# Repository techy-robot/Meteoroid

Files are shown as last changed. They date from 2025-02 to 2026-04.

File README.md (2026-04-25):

# Meteoroid


Production-ready 3d printer based on a Ender 5 frame, with multifunction tool changing, bed changing, and accessories with robots.

Preview Picture
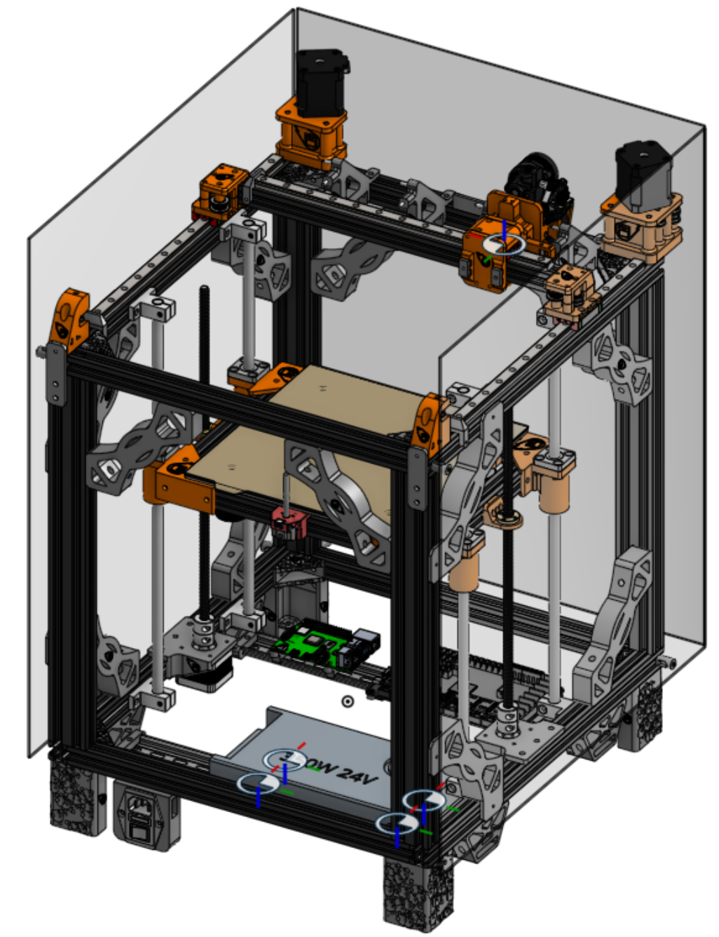
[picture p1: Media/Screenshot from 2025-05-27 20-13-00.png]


Latest V0.7.0 [Onshape Link](https://cad.onshape.com/documents/1de0655c0501c319c0be82e5/v/c2a582b56fbe86c2e3bf18a1/e/f03e8779d1a8cc2741025c01)

It is desktop machine with plug and play heads. Chain these machines together and add robot carriages in between and you got yourself an awesome modular factory that can fit on a bench. The cost of the _entire system_ will likely be several thousand dollars, with the main machine between $300 to $500. I aim to lower the cost of a complete industrial system as much as possible.

The base machine is a CoreXY printer with a 500+mm/s move speed 30k+ accel, and 4 tool changer slots. The printer can be partially enclosed, with openings for robots to quick swap tools and beds and sometimes even sub-tools (Like a PnP head with different nozzle sizes). Software-wise, it will be running Klipper, which can interface with other software like OpenPNP using macros and linux ports.

Features:
- Standard 235mm x 235mm heated bed size with Garolyte bed for easy print release, supported by dual z-axis motors to provide stabilty without the complexity of an automatic leveling trimotor bed.
- Klipper
- Tool changer with 4 slots
- CoreXY
- Medium cost desktop production system
- Completely Open-Source
- 3 Accessory slots for extra toolhead elements like PnP heads or a camera
- Off-the-shelf components that are well known and high-quality, with many parts 3D printed in ASA
- Optional enclosure
- High print speed 500mm/s and 30k accel

I also designed a little adapter board I called Klipper to CACKLE. It basically takes USB-c input and 24v power, and converts this to my [CACKLE](https://github.com/techy-robot/CACKLE) layout spec and RS485 communication protocal. It uses a CH32 chip to process the commands and output equivalent Luos spec datapackets over the bus to my system.
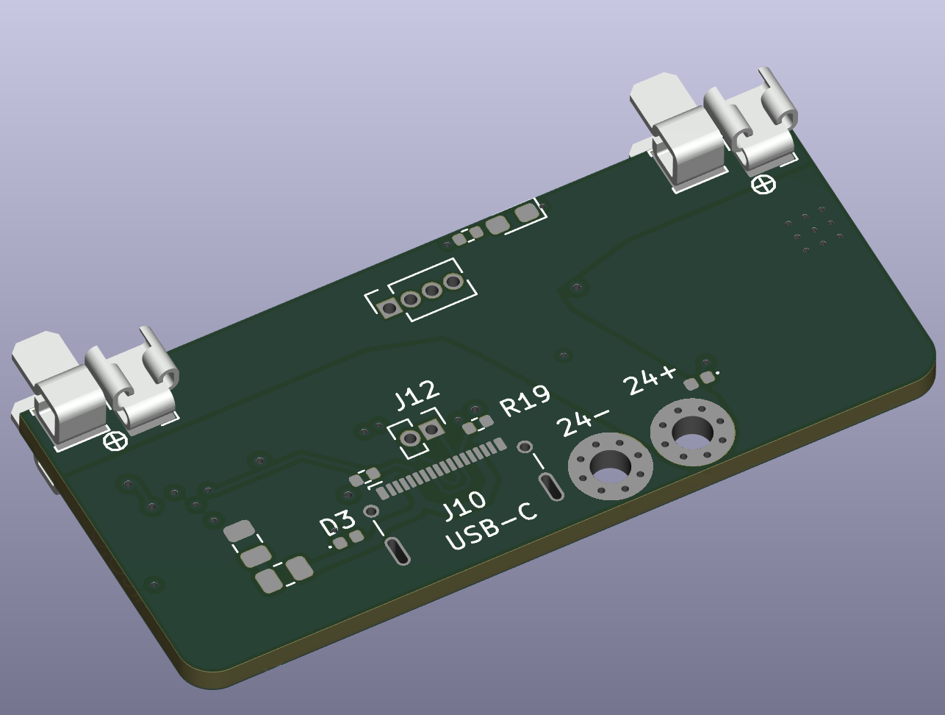
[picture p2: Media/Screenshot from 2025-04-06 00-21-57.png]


# Building
I don't have specific build instructions yet as that takes a lot more development time, but you can reference the [BOM](https://github.com/techy-robot/Meteoroid/blob/main/BOM_Main%20assembly_simplified.csv) and the CAD file/Onshape to get all the parts and build it.

# Development Log
This project was worked on sporadically since Feb 1, 2025

See [Changelog](https://github.com/techy-robot/Meteoroid/blob/main/Changelog.md) for my full development log and the nitty-gritty details

# Credits
The motion system inspiration is from [Zero G Mercury 1.1](https://docs.zerog.one/manual/build/mercury_eva), which is a relatively simple corexy conversion for ender 5-style frames. I have tweaked many of the parts to fix small issues I noticed, revamped the frame with supports, added a toolchanging solution, and a 2 axis bed leveling system instead of the more costly 3-axis Hydra solution. The toolchanger is similar to the [Daksh V2](https://github.com/ankurv2k6/daksh-toolchanger-v2/) solution, except with a simpler single lock system, and concentric kinematic mount points instead of asymetrical contact mounts.

Everything else should be my own design, from the upcoming bed changing solution, upcoming robotic arms, toolheads, and the asteroid texture used on some of the parts.

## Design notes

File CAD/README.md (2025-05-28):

This folder is for CAD documents and step files. Their is no reason to have the individual parts when there is an assembled version available, so I have only included the main assembly as well as specific toolheads. Check out the STLs folder for the individual 3D printed parts.

Also, for the sake of Github some files have been compressed.

To view the entire CAD design, checkout the latest [Onshape document](https://cad.onshape.com/documents/1de0655c0501c319c0be82e5/w/00a76129439a8316e13df1dd/e/f03e8779d1a8cc2741025c01).

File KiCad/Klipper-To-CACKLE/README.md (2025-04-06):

---
modified: 2025-04-05T19:11:32-07:00
---

# Klipper to Cackle

This is a simple adapter board PSU that takes 24v in and usb, and outputs a CACKLE compatible form factor and RS485 Luos commands.

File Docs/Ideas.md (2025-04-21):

- Add a vslot extrusion and wheels for switching off beds. Line up the rails and roll a new bed on
- Hotswap toolheads aren't supported in klipper, so either add this feature or create a macro that modifies the config and reboots klipper each toolrow swap.
- Pogo pins for USB and CAN bus between toolhead an motion carrage
- Use only USB 2.0 to communicate between MCUs because its faster than CAN bus and can support more than klipper data (like hubs and cameras). It also is easier to connect and hotswap, there aren't any resistor configuration requirements. I can use USB 3.0 for static hubs that don't change
- Design a simple converter PCB from XT60 connector and USB C, to the molex special connector
- Design hotswap pcb connectors
- Use JLCMC for all my fasteners, and mcmaster carr for other things
- Don't use Obico for failure detection, I need something on the pi like [Forgetti](https://github.com/willuhmjs/forgetti), [3d Print Sentinel](https://github.com/oliverbravery/3D-Print-Sentinel), Scythe-Spaghetti-detection or [PiNozCam](https://github.com/DrAlexLiu/OctoPrint-PiNozCam)

# Tools
dremel
spindle + drill
spindle + milling flute/ball nose mill
router bit
mini sawblade
spindle with grinding wheel / cup
tapmatic-style tap holder
shaper cutter
microscope camera
inkjet cartridge
waterjet cutter
plasma cutter
pencil
exacto holder
glass cutter
sharpie
vibropeen
lasercutter
syringe dispenser
brush + paint pots
hand file
fiber laser holder
mirror X/Y stage
plate-in-place electrode
CMM stylus probe holder
hotwire foam cutter holder
pick-and-place suction tool
soldering iron (w\ solder dispenser ?)
EDM electrode holder

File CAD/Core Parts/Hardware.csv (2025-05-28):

Name | Variable type | Value | Description
M3_screw_hole | Length | 3.15
M3_tight_screw_hole | Length | 3
M3_screwhead_hole | Length | 6
M3_heatset_hole | Length | 4.7
M3_heatset_depth | Length | 5
M5_screw_hole | Length | 5.2
M5_tight_screw_hole | Length | 4.9
M5_screw_head_hole | Length | 9
M4_screwhole | Length | 4.2
M4_screw_head_hole | Length | 8
M4_tight_screw_hole | Length | 4
M4_heatset_hole | Length | 5.7
Dowel_pin_dia | Length | 5.2
belt_width | Length | 6
belt_thickness | Length | 1.38
belt_tooth_thickness | Length | 0.75
belt_other_thickness | Length | 0.63 | the non-tooth thickness of belt
ABS_tolerance | Length | 0.2
smooth_idler_dia | Length | 13
toothed_idler_dia | Length | 12.22
belt_gap | Length | 1.5 | gap btw belt and plastic parts
smoothed_idler_9mm_flange_stack | Length | 11.2
toothed_idler_9mm_stack | Length | 9.5
motion_gap | Length | 1.5
magnet_diameter | Length | 6.35
magnet_depth | Length | 3.175
guide_with_screw_depth | Length | 1.4 | Guides are what keeps a part in alignment in an X extrusion. with nut is the depth with a screw going through it
guide_depth | Length | 4
guide_width | Length | 5.8 | width of beam, some tolerance

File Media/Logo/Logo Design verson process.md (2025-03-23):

# Inkscape Notes
- You can convert paths to filled objects using union and strokes or objects to paths and all sorts of fun combos
- If you go into object properties you can custom name SVG items!
- Use Path Combine or Break Apart tools to give paths a common stroke and color, even if they aren't connected. Boolean ops are for connections

# Process for creating Logo types
1. Create the base color logo. Use offset live path effect with rounded corners and then flatten it to a normal object for the internal light colors. More control than the Path Outset tool. Break it apart and delete the weird extra small shapes. Make sure to name all objects, and have a layer for the printer and layer for the burn
2. Copy and start on two-tone version. Delete the 3rd inset color. Make sure the color pallet only has Primary and Background colors. Change all lines to Primary color, and make sure everything else is a fill color. Re-create the burn internal offset except without internal edges. The burn has to go behind the printer now.
3. Copy and start on black and white version. Only change necessary, which should just be the colors
4. For Mono, take the path difference of the trail and the background so that you have no background fill object. Delete the fill object for the printer. Now it should be transparent and have only one color
5. Finally, to get a logo that can be extruded in 3D, convert all strokes to paths, boolean union on all paths, Get ride of all groups and layers, and save as a DXF R14 file without changing any of the defaults.

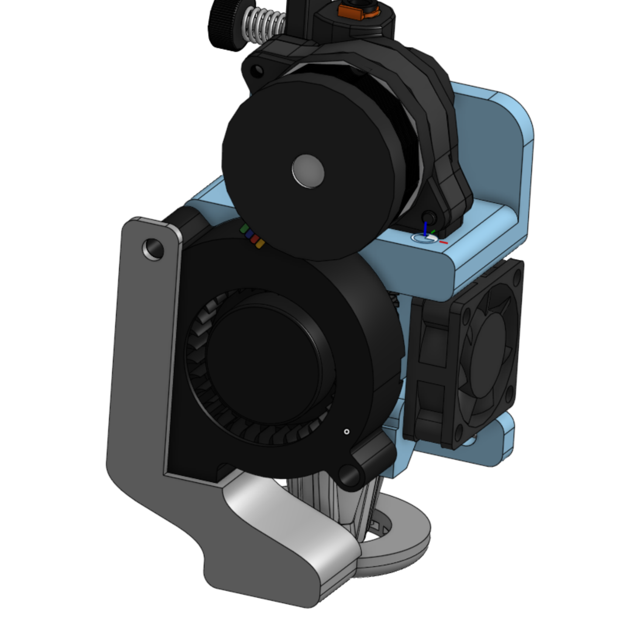
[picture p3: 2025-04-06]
Media/Screenshot from 2025-04-04 20-28-48.png

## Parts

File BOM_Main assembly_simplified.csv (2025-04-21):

ID | Quantity | Description | Name | Already have? | 3D printed | Price | Purchase Link
 | 1 |  | Left X joint bottom |  | t
 | 1 |  | Left X joint top |  | t
 | 1 |  | Right X joint bottom |  | t
 | 1 |  | Right X joint top |  | t
 | 2 |  | Z+AC0-Axis Motor Inside Bracket |  | t
 | 2 |  | bed +AC0- linear bearing mount corner |  | t
 | 2 |  | bed +AC0- linear bearing mount corner mirror |  | t
 | 4 |  | bed +AC0- frame mount |  | t
 | 2 |  | bed +AC0- lead screw nut mount |  | t
 | 4 |  | bed +AC0- thumb screw |  | t
 | 1 |  | Z endstop mount |  | t
 | 4 |  | base standoff |  | t
 | 4 |  | DIN rail drop |  | t
 | 2 |  | DIN rail clip +AC0- LRS200 LRS350 |  | t
 | 2 |  | DIN rail clip +AC0- Octopus pro |  | t
 | 4 |  | frame stiffener side mount |  | t
 | 8 |  | frame stiffener |  | t
 | 1 |  | Left Motor Mount |  | t
 | 1 |  | Left Motor Mount Top |  | t
 | 1 |  | Left Tensioner |  | t
 | 1 |  | Right Motor Mount |  | t
 | 1 |  | Right Motor Mount Top |  | t
 | 1 |  | Right Tensioner |  | t
 | 2 |  | Tensioner Plate |  | t
 | 2 |  | DIN rail clip +AC0- RPI4 |  | t
 | 1 |  | PSU switch mount |  | t
 | 1 |  | Carraige +AC0- back plate |  | t
 | 2 |  | Carraige +AC0- Belt clampx2 |  | t
 | 1 |  | Carraige +AC0- bottom |  | t
 | 1 |  | Carraige +AC0- front belt plate |  | t
 | 1 |  | Carraige +AC0- lock clamp |  | t
 | 1 |  | Carraige +AC0- lock slider |  | t
 | 1 |  | Carraige +AC0- Rail mount |  | t
 | 1 |  | Carraige +AC0- spring plate |  | t
 | 1 |  | Rapido Orbiter Toolhead +AC0- mount |  | t
 | 1 |  | Rapido Orbitor Toolhead +AC0- Duct |  | t
 | 4 |  | Tool Bay +AC0- Basic |  | t
 | 3 |  | Rail End Stop |  | t
1 | 4 | 370mm beam | 2020 extrusion 370mm | t |  | 10
 | 4 | 440 beam | 2020 extrusion 440mm | t |  | 10
 | 4 | 410mm beam | 2020 extrusion 410mm | t |  | 10
 | 2 |  | Z Stepper Ender 3 42+AC0-40 | t |  | 8.55
 | 8 |  | 10mm Clamp | t |  | 1.43
 | 4 |  | 10mm Rod | t |  | 1.41
 | 4 |  | 10mm Rod Bearing | t |  | 1.33
 | 2 |  | 5mm to 8mm Coupler | t |  | 2
 | 2 |  | TR8 Nut | t |  | 1.5
 | 2 |  | TR8 LeadScrew | t |  | 1.2
 | 1 | 2nd hand | Ender 3 Bed | t |  | 9.55
 | 2 |  | 370mm DIN rail | t |  | 7.54
 | 1 | 2nd hand | PSU Meanwell 350W 24V | t |  | 15.44
 | 1 | 2nd hand | BTT Octopus Pro | t |  | 32.44
 | 1 | 2nd hand | Raspberry Pi 4 Model B | t |  | 20
 | 1 |  | AC+AC0-01A PSU Switch | t |  | 5
 | 1 |  | 5015 Blower Fan | t |  | 5
 | 1 |  | ZeroG Mercury Fastener Kit (Includes most screws needed for XY axis) | t |  | 20.99 | https://west3d.com/products/bdf+AC0-zerog+AC0-mercury+AC0-one+AC0-ender+AC0-conversion+AC0-fastener+AC0-kit+AC0-zero+AC0-g
 | 1 |  | +ACI-Trident Gates Motion Kit (Includes pulleys | idlers | bearings and belts)+ACI- | t |  | 45 | https://west3d.com/products/west3d+AC0-bdm+AC0-trident+AC0-motion+AC0-set+AC0-silver+AC0-darkside+AC0-black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
 | 10 |  | M5x30 Shafts | t |  | 5 | https://west3d.com/products/round+AC0-shafts+AC0-5x30mm+AC0-5x60mm?variant+AD0-41971072991444
 | 1 |  | 330mm linear rail |  |  | 32.99 | https://www.fabreeko.com/products/honeybadger+AC0-mgn12c+AC0-stainless+AC0-steel+AC0-rails
 | 2 |  | 350mm linear rail |  |  | 70.58 | https://www.fabreeko.com/products/honeybadger+AC0-mgn12c+AC0-stainless+AC0-steel+AC0-rails
 | 2 |  | Nema 17 Stepper LDO 42STH48+AC0-2804AH HT |  |  | 55.98 | https://www.fabreeko.com/products/ldo+AC0-42sth48+AC0-2804+AC0-ac+AC0-ah+AC0-ahs80+AC0-super+AC0-power+AC0-motors+AC0-by+AC0-ldo
 | 2 | for bed | 2020 extrusion 230mm |  |  | 10
 | 2 | for bed | 2020 extrusion 250mm |  |  | 10
 | 20 | +ACI-Choose the S6 varient | with SUS440C material | FDWN+AC0-S6+AC0-D3+AC0-L15+ACI- | m3 x 16mm dowel pin |  |  | 5.5 | https://jlcmc.com/product/s/F02/FDWN/positioning+AC0-pin+AC0-straight+AC0-rod+AC0-h7
 | 3 | +ACI-Choose the S1 varient | with SUS304 material FDWN+AC0-S1+AC0-D3+AC0-L20+ACI- | m3 x 20mm dowel pin |  |  | 0.9 | https://jlcmc.com/product/s/F02/FDWN/positioning+AC0-pin+AC0-straight+AC0-rod+AC0-h7
 | 2 | FDWN+AC0-S6+AC0-D3+AC0-L30 | m3 x 30mm dowel pin filed down |  |  | 0.74 | https://jlcmc.com/product/s/F02/FDWN/positioning+AC0-pin+AC0-straight+AC0-rod+AC0-h7
 | 4 |  | spring OD6 ID5 Length 10mm |  |  | 1 | https://jlcmc.com/product/s/A04/ATHX/heat+AC0-temperature+AC0-compression+AC0-spring+AC0-l+ACU-C3+ACU-9740+ACU-25
 | 1 | +ACI-I already have a V2 | so I just need the upgrade kit+ACI- | LDO Orbiter v2.5 upgrade kit |  |  | 22.99 | https://west3d.com/products/ldo+AC0-orbiter+AC0-extruder+AC0-v2+AC0-5+AC0-orbiter+AC0-v2+AC0-5+AC0-and+AC0-v2+AC0-0+AC0-to+AC0-v2+AC0-5+AC0-upgrade+AC0-kit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
 | 1 |  | Rapido ACE HF |  |  | 79.99 | https://west3d.com/products/trianglelab+AC0-rapido+AC0-ace+AC0-hotend+AC0-hot+AC0-end+AC0-hf+AC0-uhf+AC0-with+AC0-104nt+AC0-or+AC0-pt1000+AC0-thermistor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
 | 1 |  | 3010 Fan |  |  | 6.49 | https://west3d.com/products/gdstime+AC0-dc+AC0-24v+AC0-30x30x10+AC0-axial+AC0-fan+AC0-24v+AC0-gda30105f+AC0-dual+AC0-ball+AC0-bearing+AC0-1200rpm+AC0-1w+AC0-0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
 | 3 | Part number EMLB+AC0-S1+AC0-M5 | m5 cap nut |  |  | 0.05 | https://jlcmc.com/product/s/E04/EMLB/cap+AC0-and+AC0-flange+AC0-nuts
 | 1 | +ACI-West3D | I will buy on my own+ACI- | ASA Orange Filament |  |  | 22.99 | https://west3d.com/products/ambrosia+AC0-asa+AC0-filament+AC0-of+AC0-the+AC0-gods+AC0-1kg+AC0-bambu+AC0-friendly+AC0-cardboard+AC0-spools+AC0-premium+AC0-3d+A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
 | 24 | for all the frame stiffeners | M3 roll in t+AC0-nut
 | 24 | for all the frame stiffeners | m3x8mm screws
 | 10 | 6x3 round magnets |  |  |  | 5
 | 6 | reed switches |  |  |  | 5
 |  |  | +ACI-TOTAL COST NEW PARTS USD SUMIF(E+ACQ-1:INDIRECT(ADDRESS(ROW() +AC0- 1 | COLUMN() | 1)) | +ACIAIgA9ACIAIg- | G+ACQ-1:INDIRECT(ADDRESS(ROW() +AC0- 1 | COLUMN() | 1)))+ACI- | 330.2
 |  |  | +ACI-TOTAL PRINTER COST USD SUM(G+ACQ-1:INDIRECT(ADDRESS(ROW() +AC0- 2 | COLUMN() | 1)))+ACI- |  |  | 543.58

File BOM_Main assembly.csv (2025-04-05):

Item | Quantity | Description | Name
1 | 1 |  | X axis
1.1 | 1 | 370mm beam | 2020 extrusion 370mm
1.2 | 1 |  | Left X joint bottom
1.3 | 1 |  | Left X joint top
1.4 | 1 |  | Right X joint bottom
1.5 | 1 |  | Right X joint top
1.6 | 1 |  | 320mm linear rail
1.7 | 2 |  | 350mm linear rail
1.8 | 4 |  | Pin 5 x 30
1.9 | 2 |  | toothed idler
1.1 | 2 |  | Single Flange Stack
1.10.1 | 2 |  | F695 Bearing (1)
1.10.2 | 3 |  | SHIM (1)
2 | 1 |  | frame and Z axis
2.1 | 1 |  | Base Frame
2.2 | 2 |  | Z Stepper
2.3 | 2 |  | Z-Axis Motor Inside Bracket
2.4 | 8 |  | 10mm Clamp
2.5 | 4 |  | 10mm Rod
2.6 | 4 |  | 10mm Rod Bearing
2.7 | 2 |  | 5mm to 8mm Coupler
2.8 | 2 |  | TR8 Nut
2.9 | 2 |  | TR8 LeadScrew
2.1 | 2 |  | 2020 230mm extrusion
2.11 | 2 |  | 2020 250mm extrusion
2.12 | 2 |  | bed - linear bearing mount corner
2.13 | 2 |  | bed - linear bearing mount corner mirror
2.14 | 4 |  | bed - frame mount
2.15 | 2 |  | bed - lead screw nut mount
2.16 | 1 |  | Bed
2.17 | 4 |  | Bed Spring
2.18 | 1 |  | Magnetic Sheet
2.19 | 1 |  | Heated Bed
2.2 | 4 |  | M4-0.7X40
2.21 | 4 |  | bed - thumb screw
2.22 | 1 |  | Z endstop mount
3 | 4 |  | base standoff
4 | 4 |  | DIN rail drop
5 | 2 |  | 370mm DIN rail
6 | 1 |  | PSU Meanwel 350W 24V
7 | 1 |  | BTT Octopus Pro Reduced
8 | 2 |  | DIN rail clip - LRS200 LRS350
9 | 2 |  | DIN rail clip - Octopus pro
10 | 4 |  | frame stiffener side mount
11 | 8 |  | frame stiffener
12 | 1 |  | Left motor mount
12.1 | 1 |  | Left Motor Mount
12.2 | 1 |  | Left Motor Mount Top
12.3 | 1 |  | Nema 17 Stepper Motor - 48mm - 1.8degree/step, 76oz-in v1
12.4 | 1 |  | Pulley 20t
12.4.1 | 2 |  | Hex socket set screw with cone point M4x0.7 x 4
12.4.2 | 1 |  | 20t 2gt Pulley 5mm
12.5 | 1 |  | Double Flange Stack
12.5.1 | 4 |  | F695 Bearing (1)
12.5.2 | 5 |  | SHIM (1)
12.6 | 1 |  | Single Flange Stack
12.6.1 | 2 |  | F695 Bearing (1)
12.6.2 | 3 |  | SHIM (1)
12.7 | 2 |  | Pin 5 x 30
13 | 1 |  | Left Tensioner
13.1 | 1 |  | Single Flange Stack
13.2 | 1 |  | Pin 5 x 30
13.3 | 1 |  | Left Tensioner
14 | 1 |  | Right motor mount
14.1 | 1 |  | Right Motor Mount
14.2 | 1 |  | Right Motor Mount Top
14.3 | 1 |  | Nema 17 Stepper Motor - 48mm - 1.8degree/step, 76oz-in v1
14.4 | 1 |  | Pulley 20t
14.5 | 1 |  | Double Flange Stack
14.5.1 | 4 |  | F695 Bearing (1)
14.5.2 | 5 |  | SHIM (1)
14.6 | 1 |  | Single Flange Stack
14.6.1 | 2 |  | F695 Bearing (1)
14.6.2 | 3 |  | SHIM (1)
14.7 | 2 |  | Pin 5 x 30
15 | 1 |  | Right Tensioner
15.1 | 1 |  | Single Flange Stack
15.1.1 | 2 |  | F695 Bearing (1)
15.1.2 | 3 |  | SHIM (1)
15.2 | 1 |  | Pin 5 x 30
15.3 | 1 |  | Right Tensioner
16 | 2 |  | Tensioner Plate
17 | 2 |  | DIN rail clip - RPI4
18 | 1 |  | Raspberry Pi 4 Model B
19 | 1 |  | AC-01A00_2_2_1_1_5_5_27_1_2_8_1
20 | 1 |  | PSU switch mount
21 | 1 |  | toolhead carriage
21.1 | 1 |  | Carraige - back plate
21.2 | 2 |  | Carraige - Belt clampx2
21.3 | 1 |  | Carraige - bottom
21.4 | 1 |  | Carraige - front belt plate
21.5 | 1 |  | Carraige - lock clamp
21.6 | 1 |  | Carraige - lock slider
21.7 | 1 |  | Carraige - Rail mount
21.8 | 1 |  | Carraige - spring plate
21.9 | 8 |  | m3 x 16mm dowel pin
21.1 | 3 |  | m3 x 20mm dowel pin
21.11 | 2 |  | m3 x 30mm dowel pin (4)
21.12 | 4 |  | spring OD6 ID5
22 | 1 |  | toolhead
22.1 | 1 |  | LDO Orbiter v2.5 v2
22.2 | 1 |  | Rapido Orbiter Toolhead - mount
22.3 | 1 |  | Rapido 2 Plus UHF
22.4 | 1 |  | 5015 Blower Fan v2
22.5 | 1 |  | 3010 Fan
22.6 | 3 |  | m5 cap nut
22.7 | 1 |  | Rapido Orbitor Toolhead - Duct
22.8 | 1 |  | m3 x 16mm dowel pin
23 | 4 |  | Tool Bay - Basic
23.1 | 1 |  | Tool Bay - Basic
23.2 | 3 |  | m3 x 16mm dowel pin
24 | 3 |  | Rail End Stop

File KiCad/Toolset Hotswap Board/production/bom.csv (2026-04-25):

Designator | Footprint | Quantity | Value | LCSC Part #
C1, C10, C9 | 0805 | 3 | 10uF | C440198
C11, C12, C2, C3, C7, C8 | 0402 | 6 | 100nF | C307331
C5 | 0603 | 1 | 47nF | C1622
C6 | 0603 | 1 | 1uF | C15849
D1, D3 | SOT-23 | 2 | BAV70 | C68978
D2, D7 | D_SOD-123 | 2 | 15v Zener BZT52C15 | C2932746
D5, D6 | D_SMB | 2 | SMBJ26A | C123820
D8, D9 | SOT-363_SC-70-6 | 2 | NUP2301 | C708740
J1, J2, J3, J4, J5, J6, J7, J8, J9 | HARWIN_S7091-42R | 9 | Harwin S7091-42R | C21394879
J10 | PinSocket_1x02_P2.54mm_Vertical | 1 | Data2 in
J11 | TerminalBlock_CUI_TB007-508-02_1x02_P5.08mm_Horizontal | 1 | dc=24 | C430601
J12 | USB_C_Receptacle_G-Switch_GT-USB-7010ASV | 1 | USB_C_Receptacle_USB2.0_16P | C2988369
Q1 | TO-252-2 | 1 | FDD86367 | C903589
Q2, Q3, Q4, Q6, Q7 | SOT-23 | 5 | BSS138 | C7420339
Q5 | TO-252-2 | 1 | SP40P04TH | C41355036
R1, R11, R12, R13, R14, R3 | 0402 | 6 | 100k | C25741
R10 | 0402 | 1 | 10ohm | C25077
R15, R16 | 0402 | 2 | 5.1k | C25905
R17, R18, R19, R20 | 0402 | 4 | 22ohm | C25092
R2, R4, R5, R6 | 0402 | 4 | 100ohm | C25076
R7 | 2512 | 1 | 4mOhm | C7420003
R8 | 0402 | 1 | 4.7k | C25900
R9 | 0402 | 1 | 27k | C25771
U1 | VSSOP-10_3x3mm_P0.5mm | 1 | TPS2491DGSR | C273636

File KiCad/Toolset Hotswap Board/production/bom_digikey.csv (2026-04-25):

Designator | Quantity | Footprint | Value | DigiKey Equivalent Part #
C1, C10, C9 | 15 | 805 | 10uF | GRM21BR61H106KE43L
C11, C12, C2, C3, C7, C8 | 30 | 402 | 100nF | CL05B104KB54PNC
C5 | 10 | 603 | 47nF | CC0603JRX7R9BB473
C6 | 10 | 603 | 1uF | CL10A105KB8NNNC
D1, D3 | 10 | SOT-23 | BAV70 | BAV70-E3-08
D2, D7 | 10 | D_SOD-123 | 15v Zener BZT52C15 | BZT52C15-E3-08
D5, D6 | 10 | D_SMB | SMBJ26A | SMBJ26A-13-F
D8, D9 | 10 | SOT-363_SC-70-6 | NUP2301 | NUP2301MW6T1G
J1, J2, J3, J4, J5, J6, J7, J8, J9 | 45 | HARWIN_S7091-42R | Harwin S7091-42R | S7091-42R
J11 | 5 | TerminalBlock_CUI_TB007-508-02_1x02_P5.08mm_Horizontal | dc=24 | TB007-508-02BE
J12 | 5 | USB_C_Receptacle_G-Switch_GT-USB-7010ASV | USB_C_Receptacle_USB2.0_16P | USB4105-GF-A
Q1 | 5 | TO-252-2 | FDD86367 | FDD86367
Q2, Q3, Q4, Q6, Q7 | 25 | SOT-23 | BSS138 | BSS138-7-F
Q5 | 5 | TO-252-2 | SP40P04TH | IPD90P04P405ATMA2
R1, R11, R12, R13, R14, R3 | 30 | 402 | 100k | RC0402FR-07100KL
R10 | 10 | 402 | 10ohm | RC0402FR-0710RL
R15, R16 | 10 | 402 | 5.1k | RC0402FR-075K1L
R17, R18, R19, R20 | 25 | 402 | 22ohm | RC0402FR-0722RL
R2, R4, R5, R6 | 25 | 402 | 100ohm | RC0402FR-07100RL
R7 | 5 | 2512 | 4mOhm | WSL25124L000FEA18
R8 | 10 | 402 | 4.7k | RC0402FR-074K7L
R9 | 10 | 402 | 27k | RC0402FR-0727KL
U1 | 5 | VSSOP-10_3x3mm_P0.5mm | TPS2491DGSR | TPS2491DGSR

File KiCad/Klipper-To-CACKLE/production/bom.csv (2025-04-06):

Designator | Footprint | Quantity | Value | LCSC Part #
C25 | 0402 | 1 | 100nF, 16v | C1525
C26 | 0603 | 1 | 4.7uF, 16v | C19666
C27 | 1206 | 1 | 22uf, 16v CL31A226MOCLNN | C159758
C28 | 1206 | 1 | 22uf, 32v | C159758
C40 | 0603 | 1 | 100nF, 16v | C14663
C7 | 0805 | 1 | 10uF, 16v | C15850
D2, D3 | 0402 | 2 | GSDH3005 | C2837790
D4 | 0603 | 1 | 2.6~3.1 Fv Green 5ma | C3028858
J1, J3, J6, J7 | Keystone_3579 | 4 | Keystone 3579
J10 | USB_C_G-Switch_GT-USB-7025-JLCPCBv | 1 | G-Switch-GT-USB-7025 | C963213
J11 | PinSocket_1x04_P1.27mm_Vertical | 1 | 1.27mm 4 pin socket
J4, J5, J8, J9 | Keystone_3569_half | 4 | Keystone 3569
L3 | 1008 | 1 | 2.2uH, WIP322512A-2R2MLDG | C5832372
R11, R29 | 0402 | 2 | 10k | C25744
R19, R33 | 0402 | 2 | 5.1k | C25905
R2 | 0805 | 1 | 2ohm | C17521
R25 | 0402 | 1 | 80.6 ohm | C185392
R26, R27, R28 | 0402 | 3 | 120 ohm | C25079
U2 | TSOT-23-6 | 1 | AP63203WU | C780769
U5 | SOT-583-8 | 1 | THVD1420DRLR
U6 | QFN-28-1EP_4x4mm_P0.4mm_EP2.8x2.8mm | 1 | CH32X035G8U6 | C7437027

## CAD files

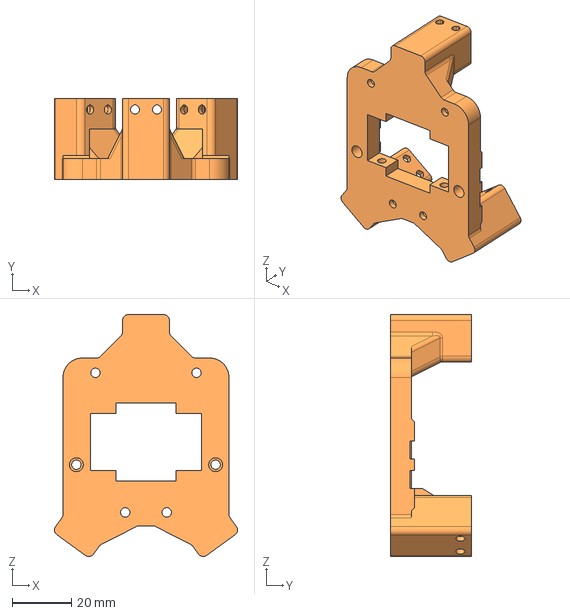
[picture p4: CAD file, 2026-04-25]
CAD/Toolhead Carraige/Toolhead carriage - Carraige - back main plate.step
61.8 x 27.2 x 81.6 mm

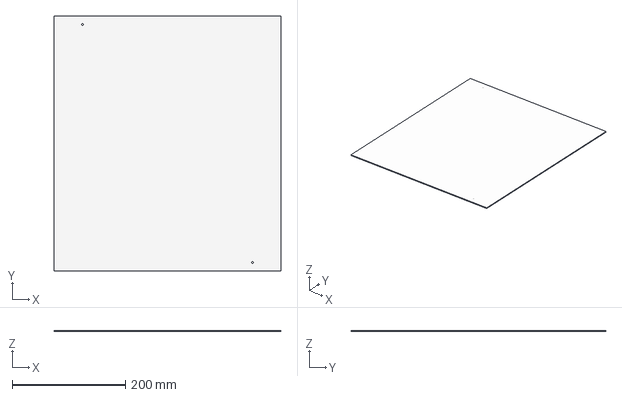
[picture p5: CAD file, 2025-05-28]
CAD/Base frame/Chamber panels/Chamber panel.step
400.0 x 450.0 x 2.00 mm

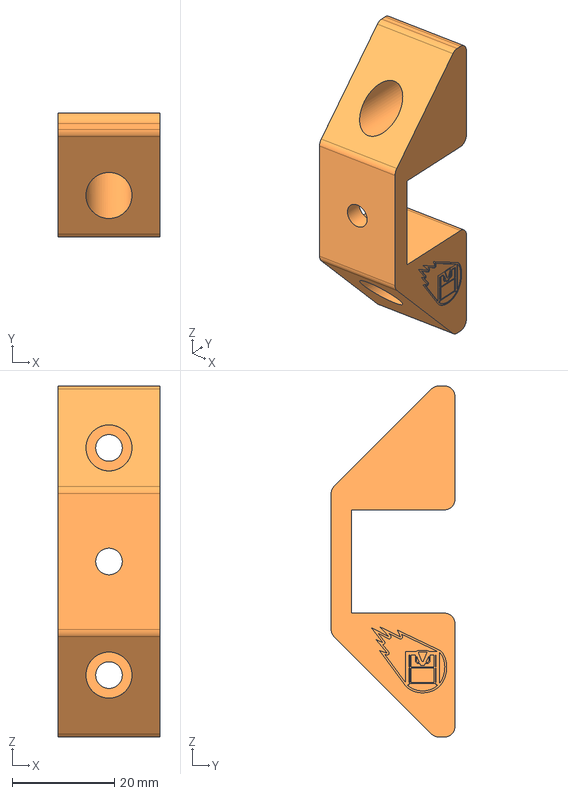
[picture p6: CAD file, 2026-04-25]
CAD/Base frame/Crossbeam mount.step
20.0 x 24.2 x 68.6 mm

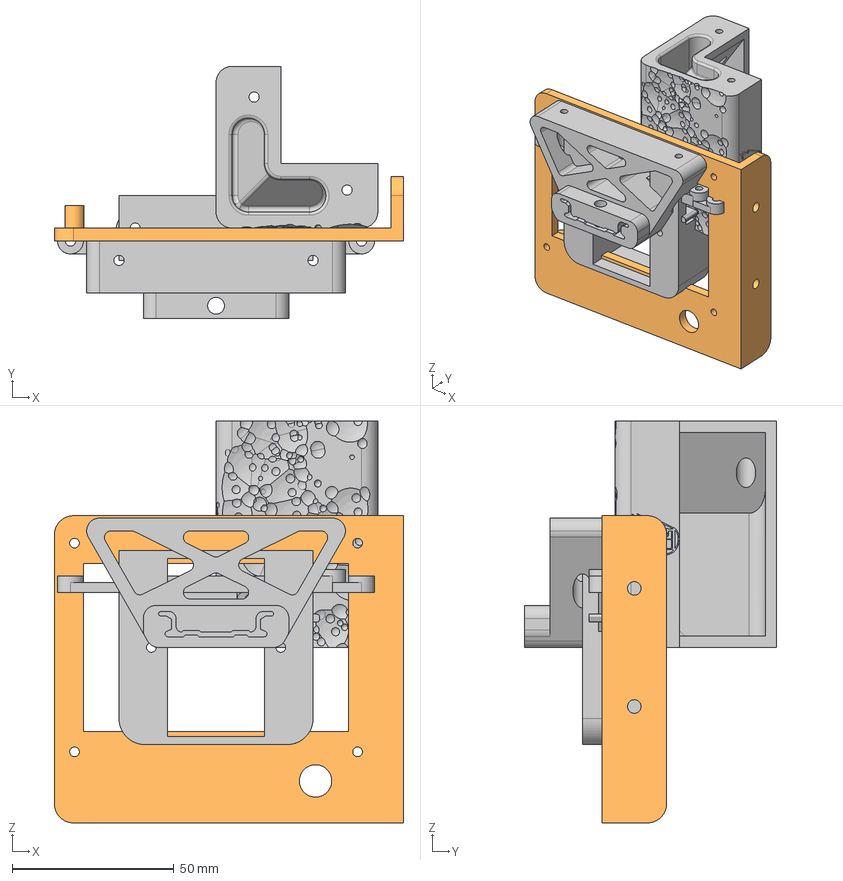
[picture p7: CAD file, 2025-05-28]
CAD/bottom electronics parts.step
108.0 x 78.0 x 124.3 mm

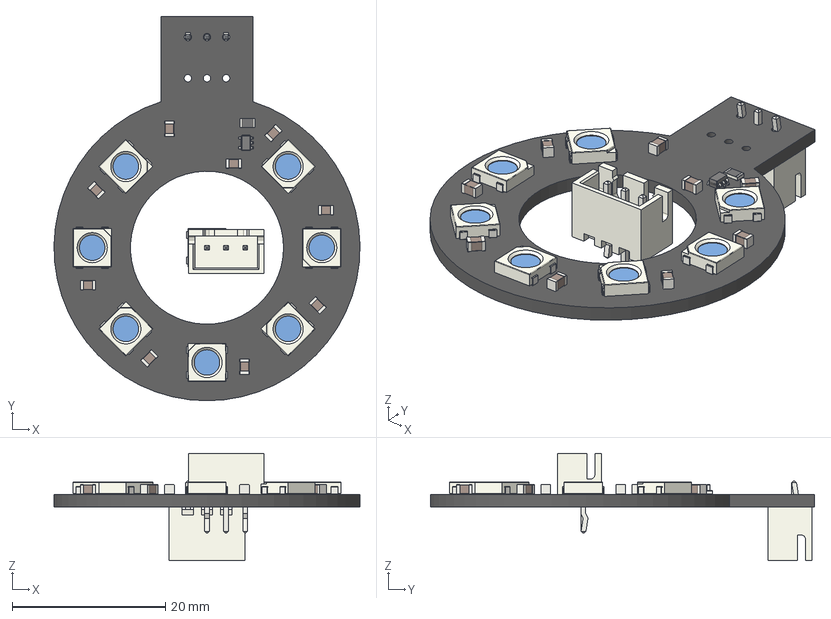
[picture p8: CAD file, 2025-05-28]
CAD/CAD Imports/top-ring-light.step
40.0 x 50.2 x 14.1 mm
X_Axis x 63
XZ_Plane x 63
bottom-ring-ligh-pcb001 x 2
Sketch

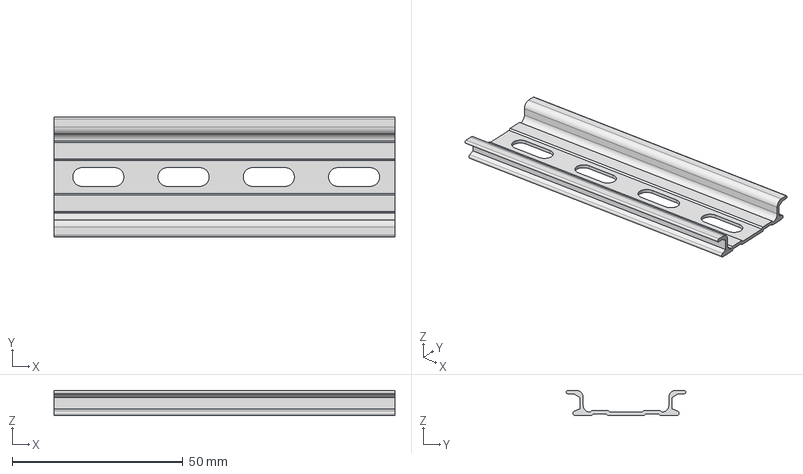
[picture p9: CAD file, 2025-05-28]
CAD/Core Parts/Configurable DIN rail.step
100.0 x 35.1 x 7.45 mm

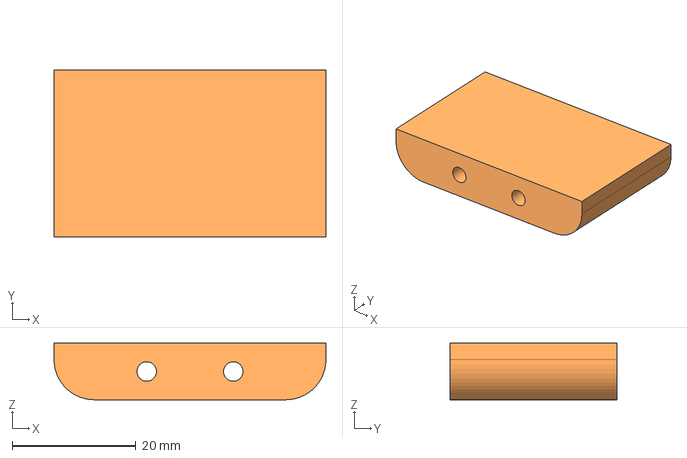
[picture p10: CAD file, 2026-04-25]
CAD/Toolhead Carraige/Toolhead carriage - Carraige - bottom.step
44.0 x 27.0 x 9.15 mm

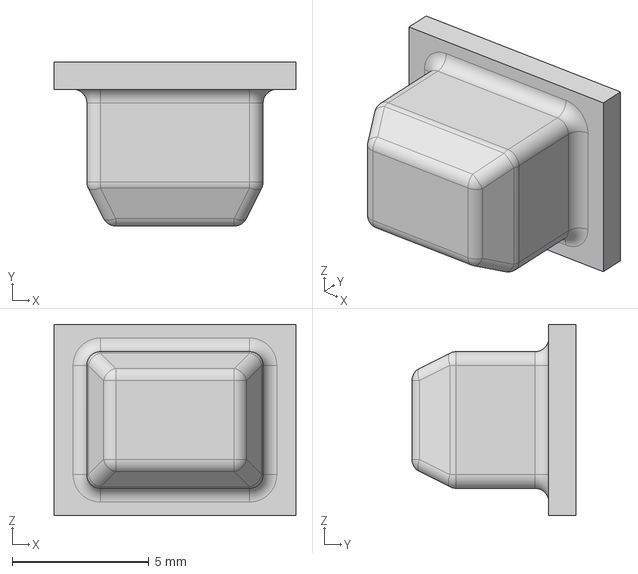
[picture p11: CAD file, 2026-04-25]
CAD/Toolsets/Base/Base Tool - spring keeper insert.step
8.85 x 6.00 x 7.00 mm

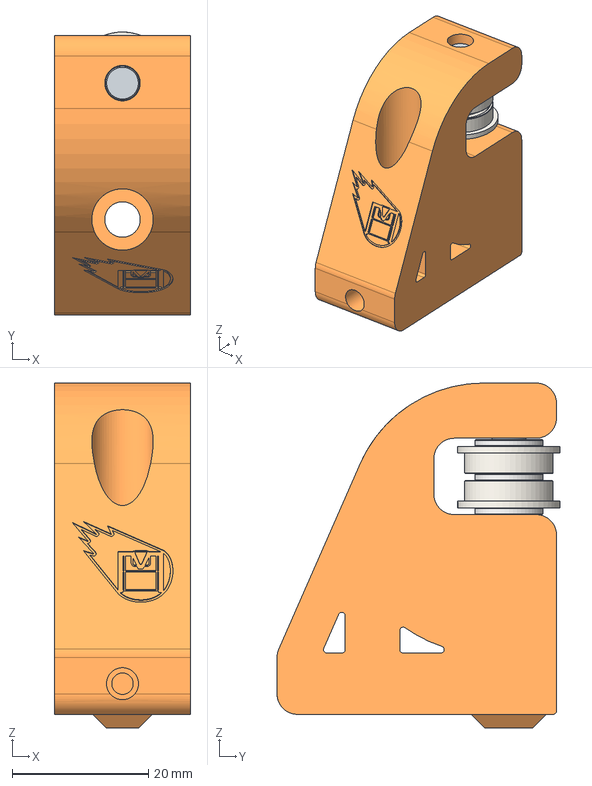
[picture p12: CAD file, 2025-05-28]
CAD/XY axis/Right Tensioner.step
20.0 x 41.5 x 50.6 mm
Right Tensioner
SHIM (1) x 3
F695 Bearing (1) x 2
Pin 5 x 30

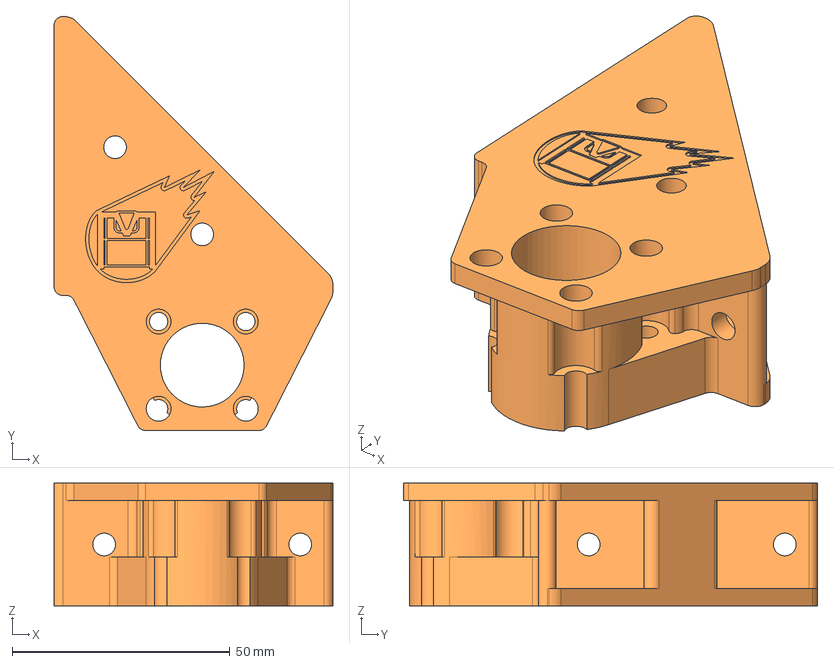
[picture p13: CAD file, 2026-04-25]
CAD/Z axis/bed frame parts/bed frame parts - bed - linear bearing mount corner mirror.step
64.0 x 95.0 x 28.2 mm

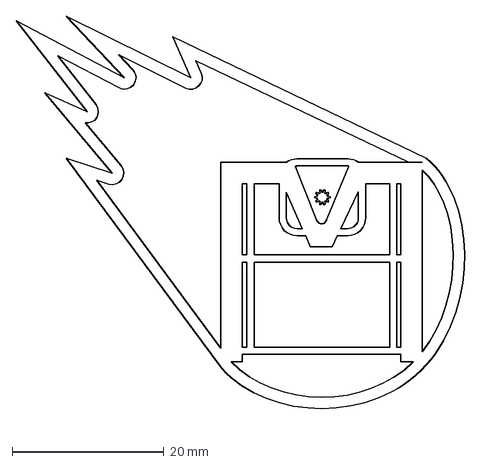
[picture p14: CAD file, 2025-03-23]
Media/Logo/Meteoroid-logo-3DP.dxf
61.2 x 53.9 mm

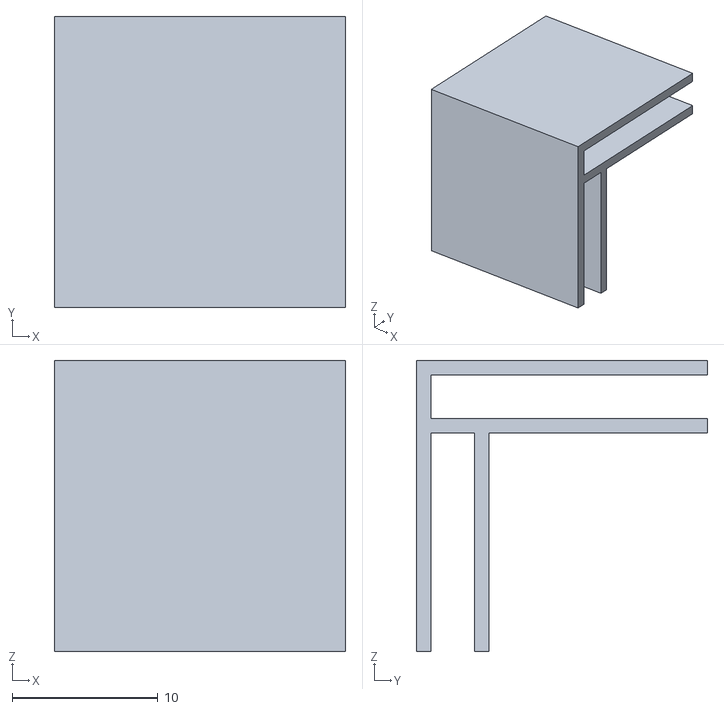
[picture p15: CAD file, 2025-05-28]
STLs/Base frame/Chamber panels/chamber panel attachments - chamber panel clip x10.stl
20.0 x 20.0 x 20.0

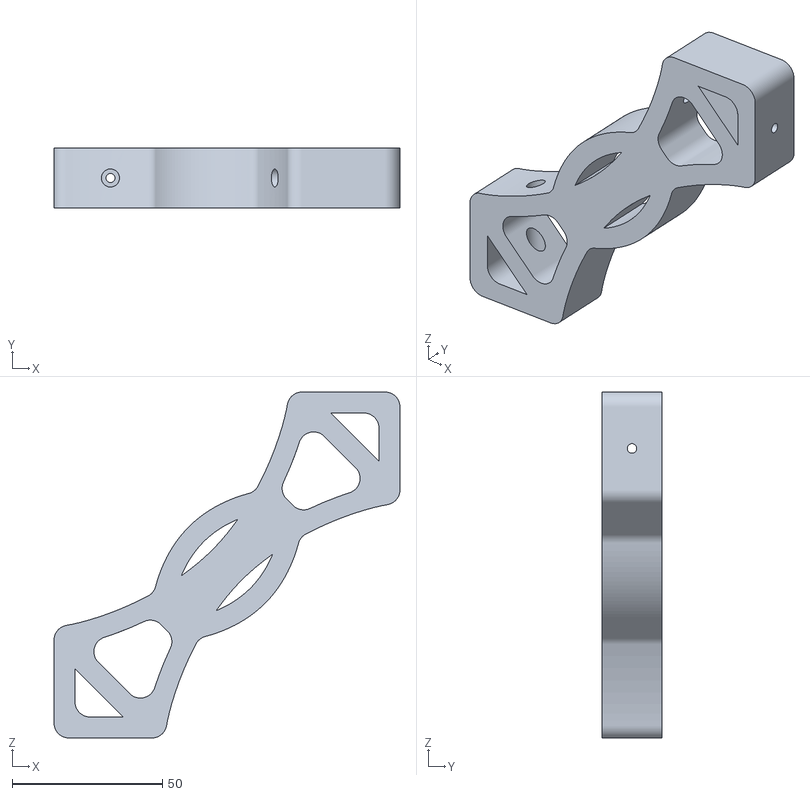
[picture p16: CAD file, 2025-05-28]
STLs/Base frame/frame stiffeners/frame stiffeners - frame stiffener x8.stl
115.0 x 20.0 x 115.0

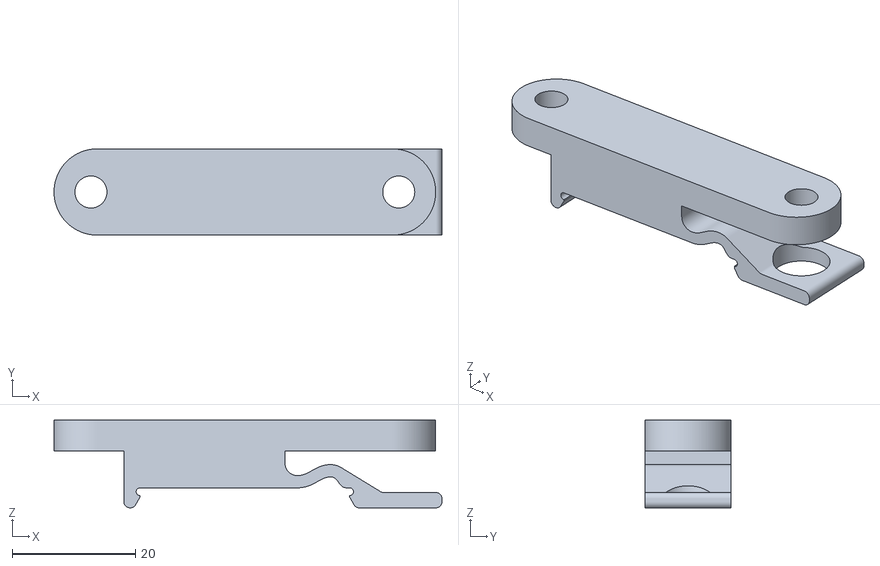
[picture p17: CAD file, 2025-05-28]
STLs/bottom electronics parts/bottom electronics parts - DIN rail clip - LRS200 LRS350 x2.stl
63.0 x 14.0 x 14.3

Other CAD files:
STLs/Reprints.3mf
STLs/Toolbay/Tool Bay - Basic - Tool Bay - Basic x3.stl
STLs/Toolhead/CRtouch Bed Probe - CRtouch Bed Probe.stl
STLs/Toolhead/Nema 11 PNP head/Nema 11 PNP head - ring light holder.stl
CAD/Base frame/Base Frame.step
CAD/Base frame/Chamber panels/chamber panel attachments.step
CAD/Base frame/corner stiffeners.step
CAD/Base frame/frame stiffeners.step
CAD/CAD Imports/ELP-USB100W03M camera.step
CAD/CAD Imports/MGN12 Rail 350mm.step
CAD/CAD Imports/lumen PNP head.step
CAD/Core Parts/Extrusions.step
CAD/Core Parts/Special Extrusions with holes.step
CAD/Core Parts/calibration part.step
CAD/Core Parts/meteor texture.step
CAD/Toolhead Carraige/Toolhead carriage - Carraige - Belt clampx2.step
CAD/Toolhead Carraige/Toolhead carriage - Carraige - Rail mount.step
CAD/Toolhead Carraige/Toolhead carriage - Carraige - lock plate.step
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

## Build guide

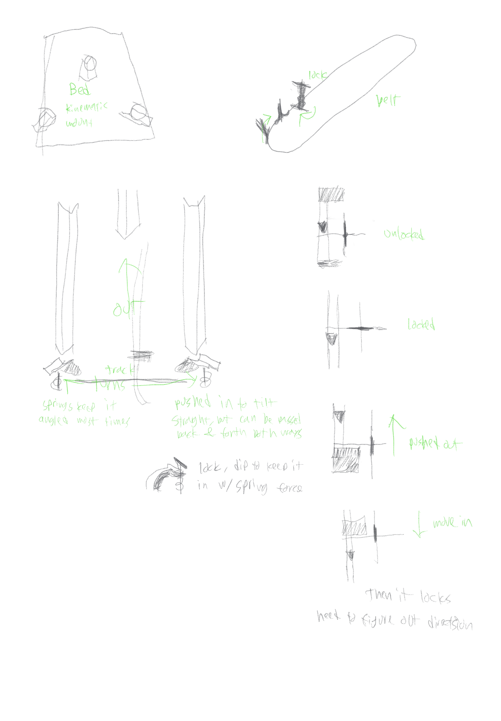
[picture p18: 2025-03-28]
Media/2025-03-26 3D printer bed swap ideas.tiff

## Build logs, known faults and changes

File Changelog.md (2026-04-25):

---
modified: 2026-04-24T23:28:50-06:00
---
Made by: @techy-robot

Repository link: https://github.com/techy-robot/Meteoroid

Total hours so far: 98.5 hrs

- [x] I have a 3D printer or will be getting one before March 21st

# Overview
Production-ready 3d printer based on a Ender 5 frame, with multifunction tool changing, bed changing, and accessories with robots.
https://github.com/techy-robot/Meteoroid

It is desktop machine with plug and play heads and beds. Chain these machines together and add robot carriages in between and you got yourself an awesome modular factory that can fit on a bench. The cost of the _entire system_ will likely be several thousand dollars, with the main machine between $300 to $500. I aim to lower the cost of a complete industrial system as much as possible.

The base machine is a CoreXY printer with a 500+mm/s move speed 30k+ accel, and 4 tool changer slots. The printer is partially enclosed, with several openings for robots to quick swap tools and beds and sometimes even sub-tools (Like a pnp head with different nozzle sizes). Software-wise, it will be running Klipper on a RPI zero 2w, which can interface with other software like OpenPNP using macros and linux ports.

Goals/Requirements:
- Standard 235mm x 235mm heated bed size with Garolyte bed for easy print release, supported by dual z-axis motors to provide stabilty without the complexity of an automatic leveling trimotor bed.
- Klipper
- Tool changer with 4 slots
- CoreXY
- Medium cost for a desktop production system
- Completely Open-Source
- 3 Accessory slots for extra toolhead elements like PnP heads or a camera
- Off-the-shelf components that are well known and high-quality, with many parts 3D printed in ABS
- Enclosed
- High speed 500mm/s and 30k accel
- High Quality

Project Time Span: Feb 1, 2025-Present

# Log
This is a log of every day I have worked on this project

## Finished exploration of push push linear design and moving to barrel CAM push-push April 24, 2026

The old design was a linear track. I actually tried about 20 different varients of the heart shaped CAM, you can see the final version CAD model below. It just kept binding.

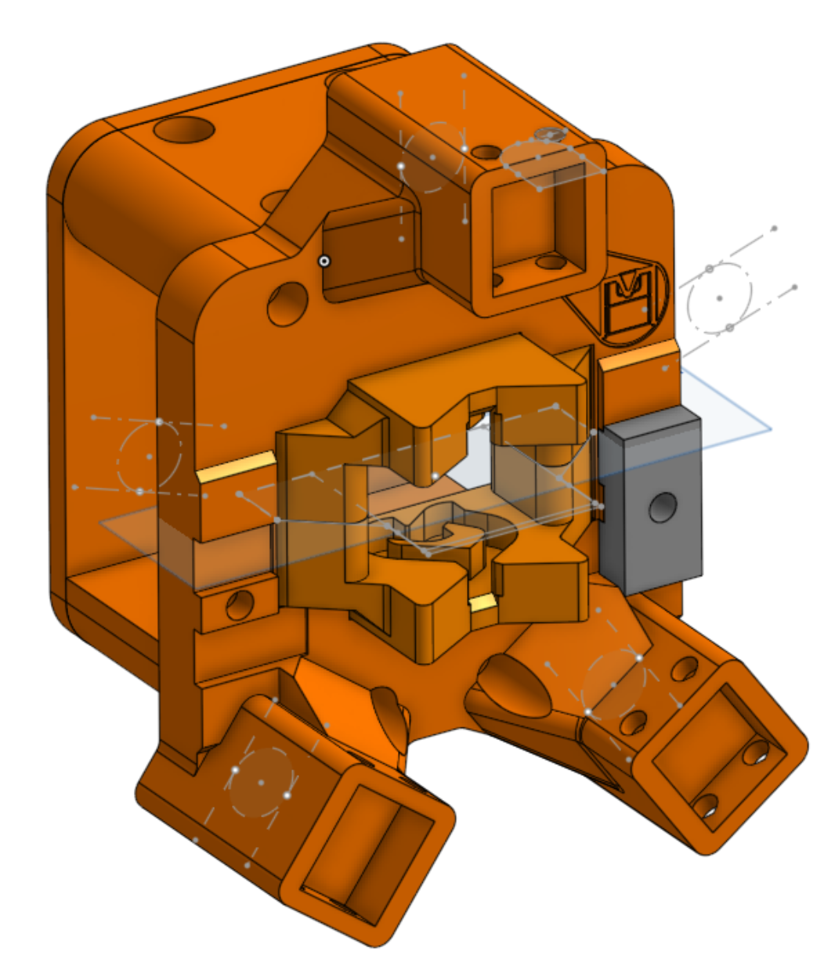
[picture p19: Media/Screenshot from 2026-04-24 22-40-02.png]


The new version I am working on uses magnets for hysterics and holding forces, which is new terrain. This is combined with a rotating barrel cam design that will actually rotate and lock the tool when pushed.

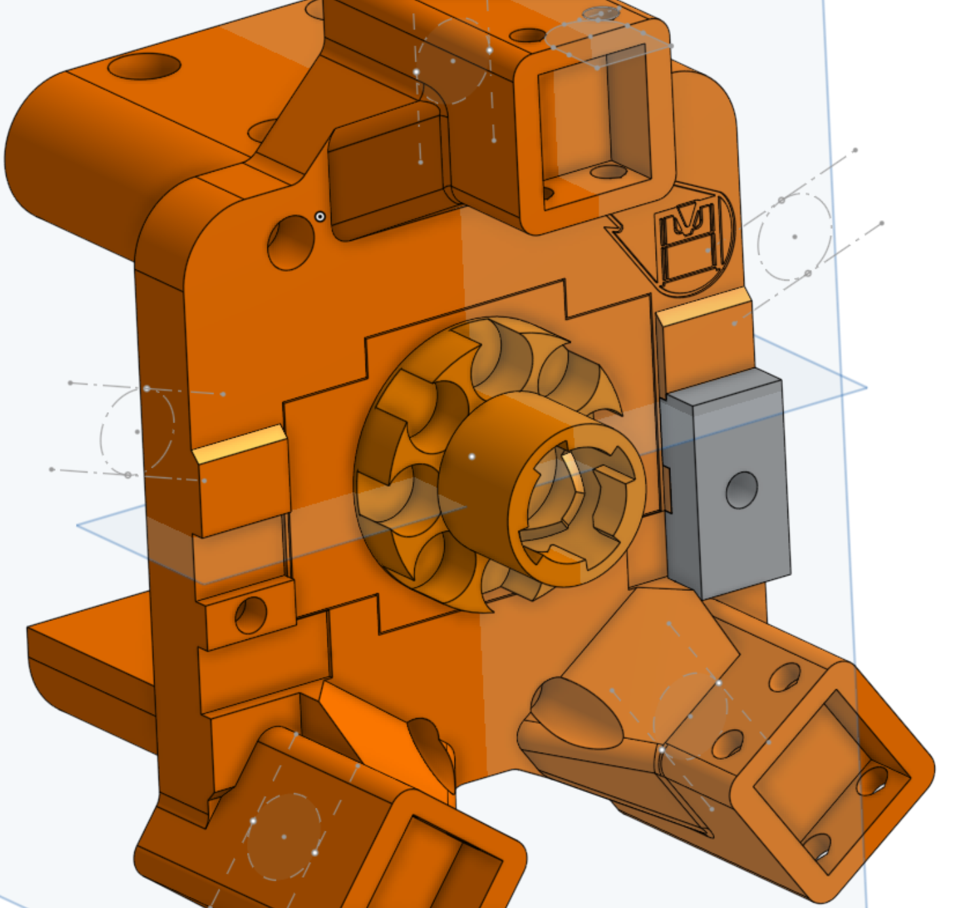
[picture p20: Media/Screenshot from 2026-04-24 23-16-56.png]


[Onshape Link](https://cad.onshape.com/documents/1de0655c0501c319c0be82e5/w/1baf60f0f4edbe4563b81650/e/f4a197586fc46ac1237943ae)

Time: 2 hrs

## Designing Push Push toolchanger mechanism June 19, 2025

I spent some time today designing a new toolhead lock, a spring action push push lock!

## Released v0.7 May 27th, 2025

This version is essentially the printer that I showcased at RMRRF. Toolchanging has not been setup, and in fact the locking mechanism itself fails with high vibrations. I should have released this before the event.

New Features:
- Pnp Toolhead
- CRTouch head
- LCD display mount
- Backing wall for all toolheads

Fixes:
- Fixed X joints config error introduced in v0.5.3
- Fixed Assembly mates
- Adjusted build plate frame parts
- Redo corner stiffeners for M5 screws and adjusted distance
- Changed Z endstop to be side mounted instead of top mounted
- Aligned toolhead kinematic mount to have proper 45 degrees contact angle
- Cutout more plastic in hotend cooling fan mount to increase airflow



[Onshape Link](https://cad.onshape.com/documents/1de0655c0501c319c0be82e5/v/c2a582b56fbe86c2e3bf18a1/e/f03e8779d1a8cc2741025c01)

Time: 1 hr

## RMRRF Day 2 - May 18th, 2025

Day 2 my printer was working! I could relax finally, put it at the front of the table, and explore the venue. There were A LOT of interesting booths, and I got some pictures with a few youtubers. I also got inspiration for new toolchanger designs, such as Misschanger, and an unidentified one with round door latch style of lock.

Some group pictures:

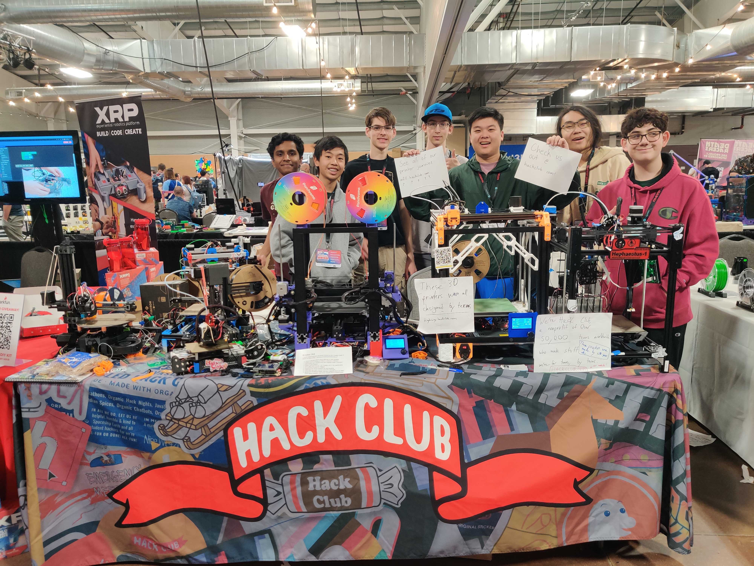
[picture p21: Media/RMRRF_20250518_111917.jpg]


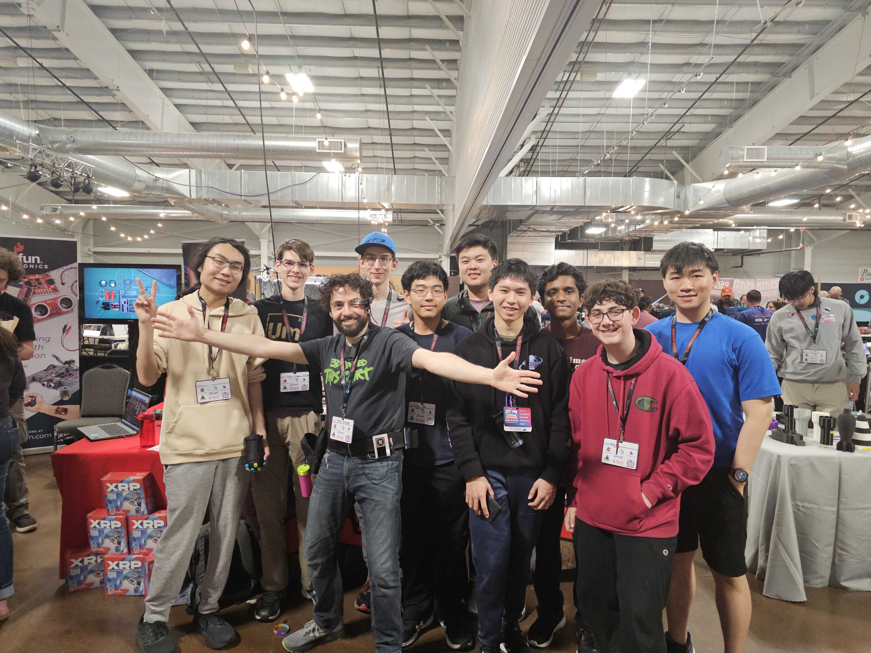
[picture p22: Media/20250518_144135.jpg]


## RMRRF Day 1 - May 17th, 2025

Most of the day I was working on my printer in the HackClub booth, in the back. I missed quite a few give-a-ways and youtubers stopping by.

In the middle of the day my replacement control board arrived, so I drove back to the airbnb to retrieve it, as well as to get some parts for other hack club members.

I finally got the printer up and running, and I have determined that the sensorless homing is absolutely a driver issue. Swapping out the MKS TMC2209 drivers for BTT TMC2209 drivers with another Hackclubber solved my problems and I could get readings.

I stayed up till 1:30 am getting my printer somewhat opperational back at the house.

Time: 8 hrs.

## Driving & setup - May 16th, 2025
Today I packed everything and drove up to the event to meet up with other Hackclub members and get setup.

I didn't spend much time on the printer itself, only a little bit setting up a wifi hotspot on the RPi.

Time: 30 min

## Shorted Motherboard! - May 15th, 2025
I was very foolish today. While configuring klipper and runnign tests I couldn't get sensorless homing to work and I tried everything. I removed one of the drivers to identify the manufacture of the TMC2209 (it was Makerbase). This might of been my problem, but the system was still on when I plugged it back in. In an instant their was a snap sound, a spark, and smoke appeared from somewhere. The short circuit alarm started going off and the raspberry pi 4 shut off.

I inspected the board and the driver, and there was a blown op amp chip on the signal lines for the socket, and the driver chip had a hool in it as well. Remarkably the RPi was perfectly fine booting separately, so I didn't dare plug it back in to do a power test with the main board. The main board power test did not go well, no alarms this time but the STM32 chip rapidely heated up too hot to touch, so shut it off.


The most likely thing that happend was I plugged in the step stick driver offset by one, connecting the 2 ground pins on the driver to the 5v and the 24v pins on the board.

I rapidely ordered a replacement, because this weekend is RMRRF! It should be delivered on May 17th at the airbnb I'm staying at for the event. I also bought a few extra parts, like screws, copper brushes, a PTC car heater, and air filters. These will be future upgrades, all I definitely need is the control board.

Time: 4 hours 

## Some Assembly - May 12th, 2025

I finished a lot of the assembly tonight, including replacing some of the toolhead parts again, and adding backing walls.

Time: 2 hours

## May 11th, 2025

I discovered an interesting way to attach the chamber mounts: Pull tightly and spin in. I didn't design the attachment properly but it still ended up working fine. 

Time: 30 min

## Redesigned toolhead - May 4th, 2025 

I spent the past 2 days and today redesigning my toolhead. It now has a BTT EBB36 mount and much better ducts

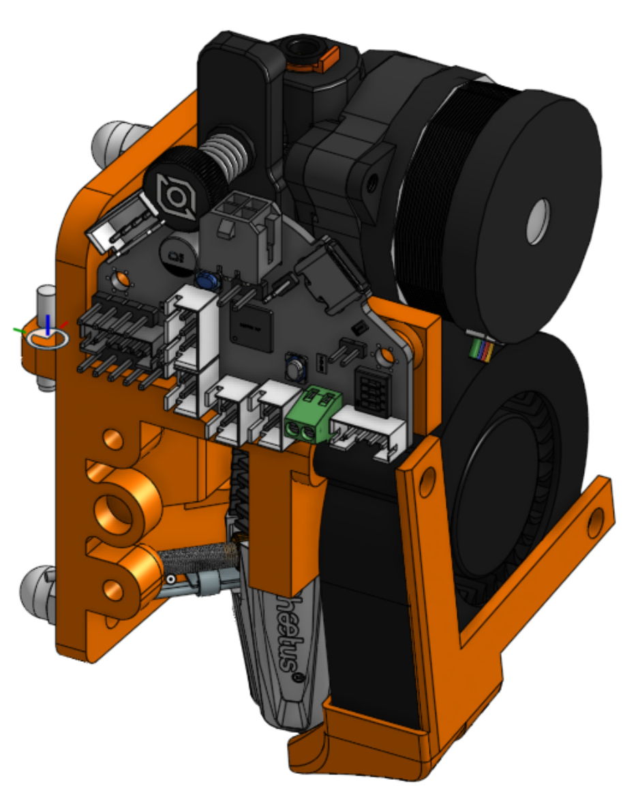
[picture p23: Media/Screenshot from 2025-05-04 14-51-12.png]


Time: 10hrs

## All Pikes Peak Makes - April 26th, 2025

Today I attended the All Pikes Peak Makes maker faire at library 21c! It was great, I got to share all my projects including my 3D printer, along with my brother. We advertised Hack Club as well, with a lot of potential signups. I tuned my printer live at the event, and managed to print a bad benchy at 350mm/s. I still need to completely replace the parts and add the toolchanging head.

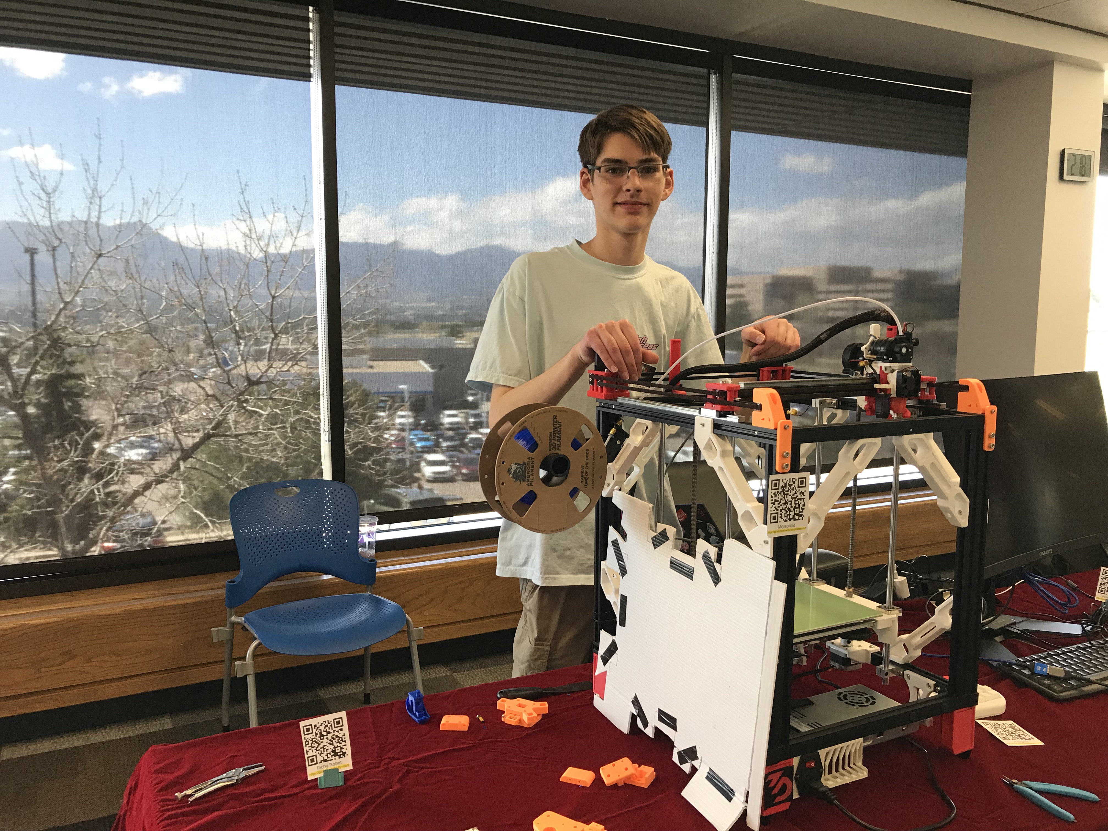
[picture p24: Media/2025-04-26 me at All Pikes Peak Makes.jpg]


Time: 7 hrs

## Prep for event tommorow - April 25th, 2025

I spent awhile building sub-assemblies and trying to make my printer functional for tomorrow. I ended up not finishing the entire new assembly, and since my new printer is similar enough to my old printer, I decided to replace some compatible parts and leave the rest. I managed to cut myself multiple times extracting the bearing towers from the old parts.

All I ended up doing: Set up the RPi4 completely with klipper, attach it, and replace the front towers.

Time: 5 hrs

## Printed all the parts - April 24th, 2025
All my parts are printed, there was a lot of trial and error initially printing the orange ASA, I had to make sure my chamber was sealed and all fans were off.



Time: 3 hrs

## Parts Arrived! - April 19th, 2025
All my important parts arrived! Some parts are going to be reused from old projects as well, which aren't shown here



Time: 30 mins

## Ordering Parts! - April 11th, 2025

Today I ordered a majority of my parts! It took a lot longer than expected, and I still haven't orderd my complete BOM. I only ordered "the big items," like hotend, motors and extruder.

Time:2 hrs

## April 6th, 2025

After some conversations with other members of the 3D printer community, some felt that the XY motion system design is too close to the original ZeroG mercury printer design. I have decided to make some modifications to the look without impacting functionality.

New XY gantry pictures:

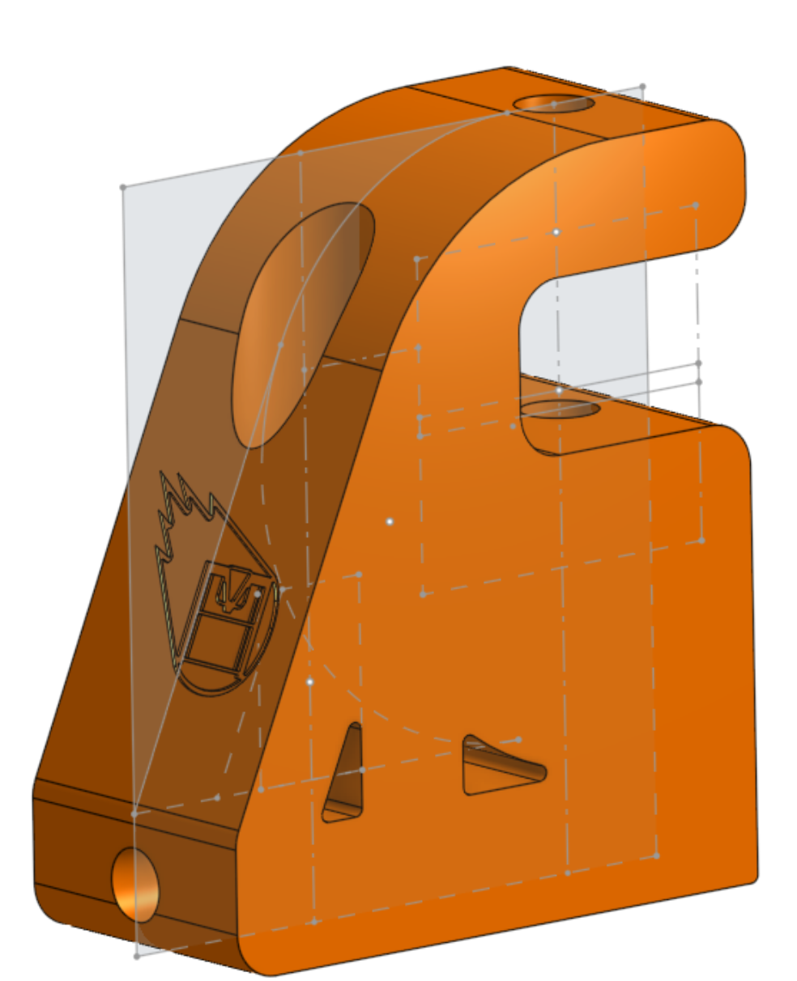
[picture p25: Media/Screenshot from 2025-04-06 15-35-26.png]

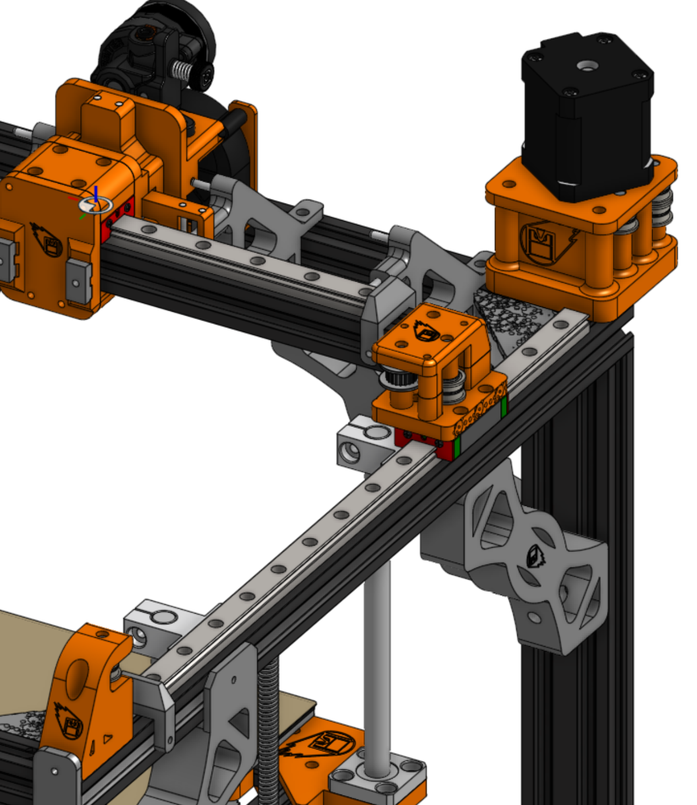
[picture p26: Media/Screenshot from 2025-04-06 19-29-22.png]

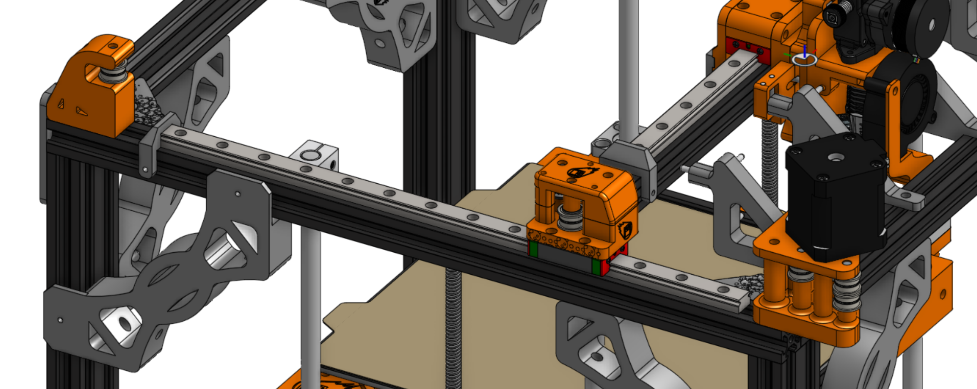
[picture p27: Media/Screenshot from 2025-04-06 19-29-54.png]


I also want to show some clarity on how my toolchanger design is different and improves on Daksh V2

Pictures to start:
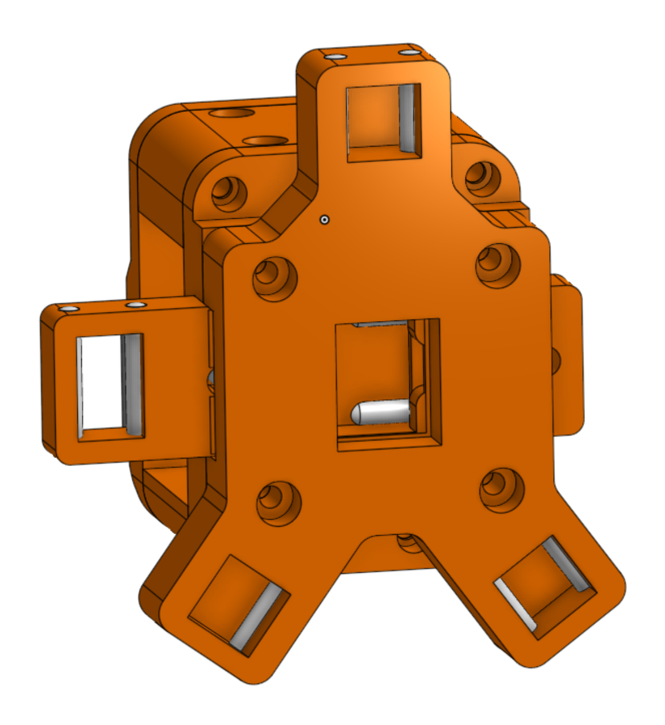
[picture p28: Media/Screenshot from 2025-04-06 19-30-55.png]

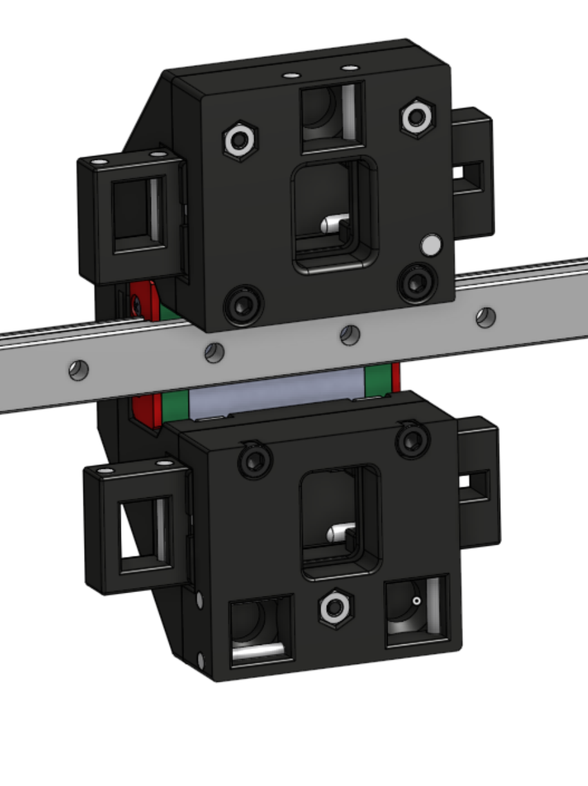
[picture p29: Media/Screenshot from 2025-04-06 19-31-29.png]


My design is a single lock system that is *centralized,* all the force applied by  thelock is put in the direct center of the kinematic mount, distributing the force evenly. Daksh V2 has two separate locks, one on the top and one on the bottom, applying an equal amount of spring force on unequal mounting.

I also noticed in the Daksh v2 toolhead that two of the three mounting points have the rods facing vertically, and the 3rd horizontally. I am concerned that this adds a small amount of uneven rotation to the system. If you look up normal kinematic mounts, the V-grooves are pointed in towards the center, and restrict all degress of freedom. Having each mount point facing a different direction likely applies uneven force. I wanted to fix that.

Time: 4 hrs

[Onshape Link](https://cad.onshape.com/documents/1de0655c0501c319c0be82e5/v/472a7a2f31d89b23ef308c6a/e/f03e8779d1a8cc2741025c01)

## Released first version 0.5 (for Hackclub Infill at least) - April 5th, 2025

I made a lot of small design tweaks to get things to fit on the tool change, or other.

I designed a RPI mount, and endstops and docking places as well.

I also switched to an inset 3010 fan for the hotend to reduce horizontal space taken, which should save 10mm. I really want to fit 4 tools in!

I have exported all the sub-assemblies that I think are important and put them into the same folder structure as found on onshape. I left out some small part assemblies that are found in later big assemblies to save space.

To print actual parts, see the STLs folder, though you could always pick out individual parts from the STEP assemblies.

This is release V0.5, as I have not tuned any of the parts to work with ASA, or revised my design with things that didn't work.
[Onshape Link](https://cad.onshape.com/documents/1de0655c0501c319c0be82e5/v/822dbc763cf3844d6902b3b4/e/f03e8779d1a8cc2741025c01)

BOM is also finished.

I designed a little adapter board I called Klipper to CACKLE. It basically takes USB-c input and 24v power, and converts this to my CACKLE layout spec and RS485 communication protocal. It uses a CH32 chip to process the commands and output equivalent Luos spec datapackets over the bus to my system.


Final picture
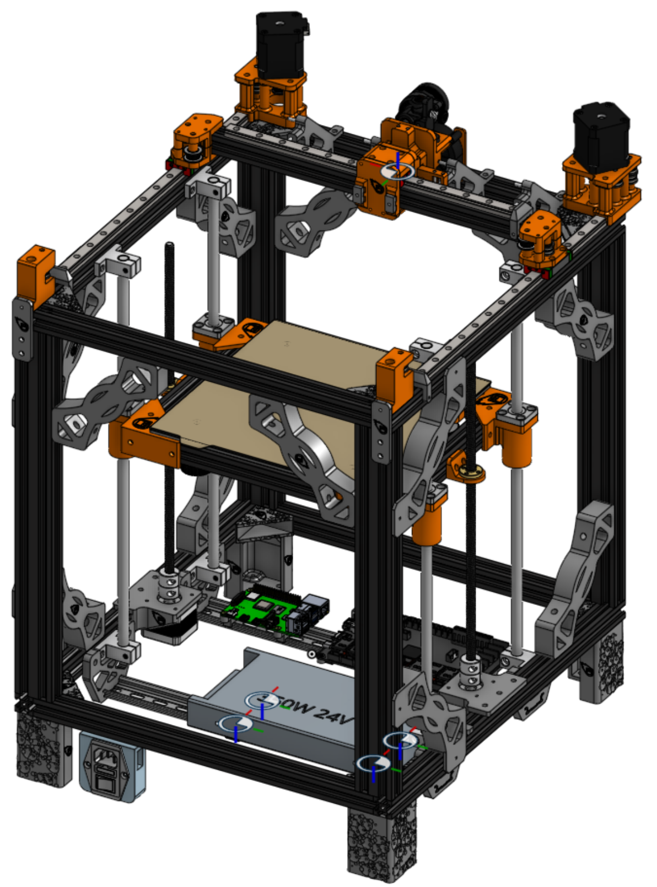
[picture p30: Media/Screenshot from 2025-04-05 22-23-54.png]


Time: 6 hrs

## Finished first toolhead - April 2, 2025

Finished my first toolhead!

Fan air path cutaway
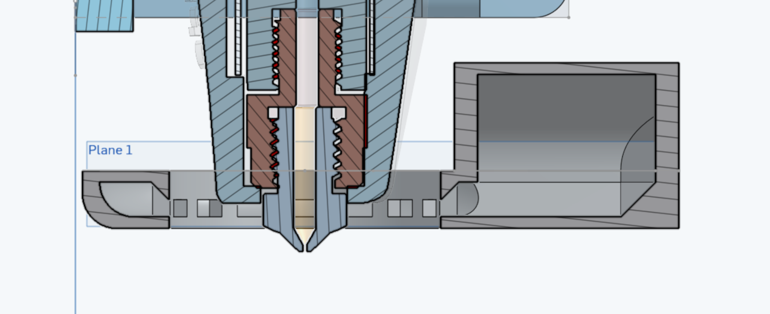
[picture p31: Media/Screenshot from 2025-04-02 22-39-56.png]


Finished toolhead, with a Phaetus Rapido 2.0 UHF, Orbiter 2.5, a 5015 blower, and a 4010 hotend fan.
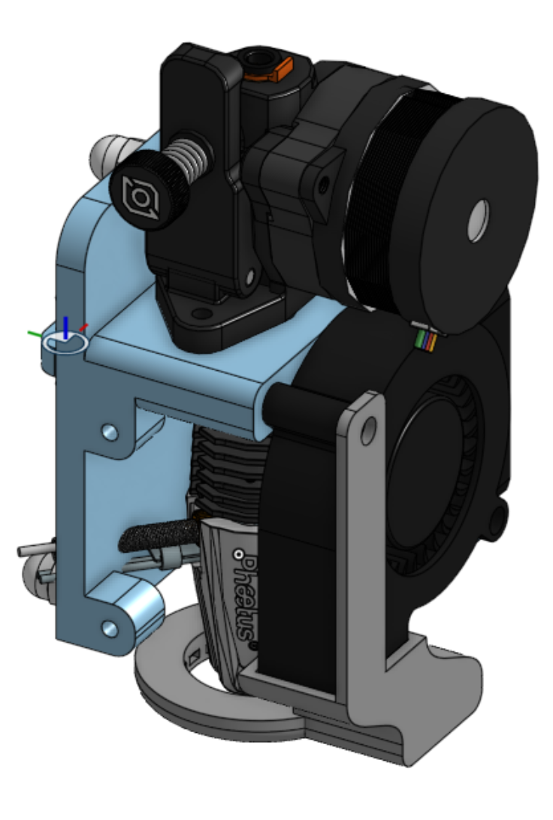
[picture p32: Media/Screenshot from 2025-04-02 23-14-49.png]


[Onshape Link](https://cad.onshape.com/documents/1de0655c0501c319c0be82e5/w/00a76129439a8316e13df1dd/m/c52a5d6f06725d51ee408f74/e/9f1bf3c1958c2faa9304390e)

Time: 2 hrs

## Finished Assembly of Toolhead carriage - March 31, 2025
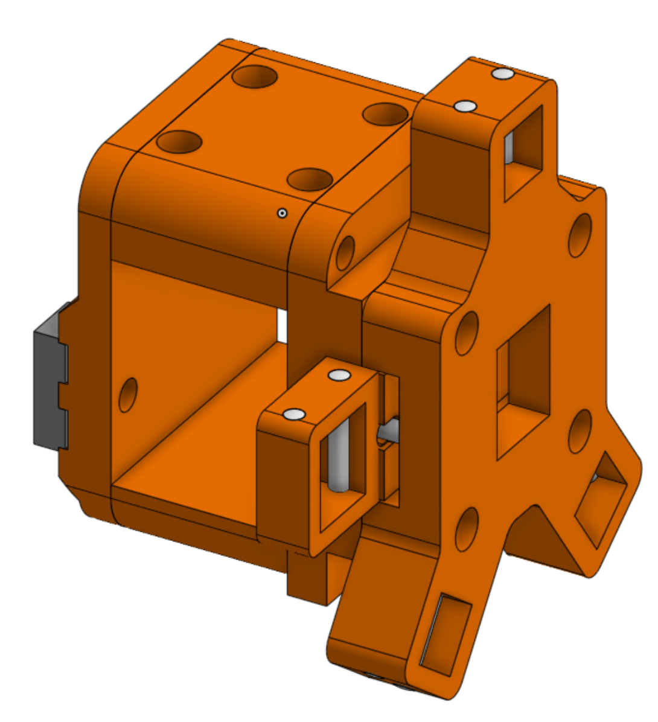
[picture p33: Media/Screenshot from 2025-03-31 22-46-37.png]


Time: 1hrs

## Finished Toolhead carriage and lock - March 29, 2025

Now I need an actual toolhead, a PCB design and the BOM. So close to completion!

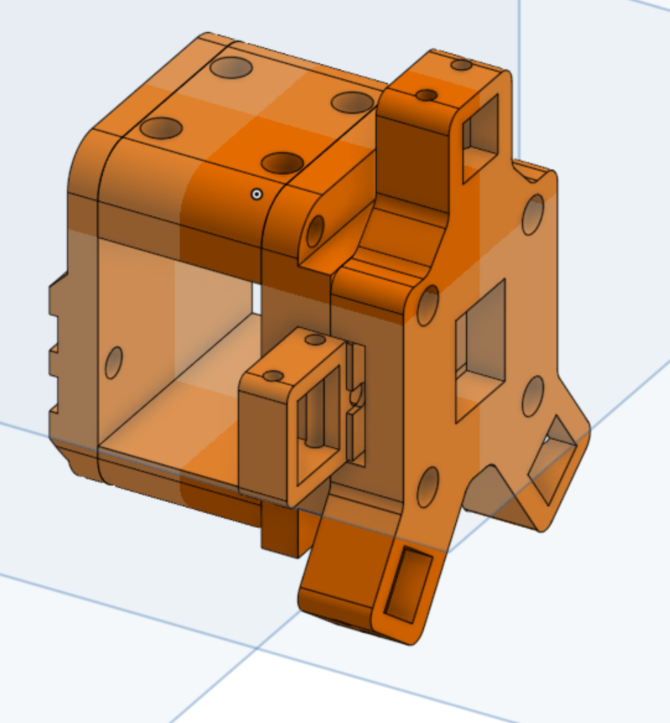
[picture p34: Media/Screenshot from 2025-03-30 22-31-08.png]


[Onshape Link](https://cad.onshape.com/documents/1de0655c0501c319c0be82e5/w/00a76129439a8316e13df1dd/m/95975a92215106d46bcc167e/e/5035fd16eb1a96461381da20)

Time: 3 hrs

## Finished top motion system - March 28th, 2025

I finished designing all the motion system parts today. Only the toolhead and extra little parts left now! The toolhead is going to be complex still, and I may need to change my gantry back to the rail being mounted in front instead of on top. The Prusa XL has front mount rail, and so does Daksh V2.

I realized that my frame was the wrong shape! It was supposed to be 410 by 440, not 410x410 ! I also spent about an hour fixing other random dimension errors or things I missed.

I added my updated logo design to several parts as well. I only put logos on parts that are personalized or parts that I can reasonably claim my own. Several of the motion parts are *based* on other's works and I can't plaster my logo on it and erase credit if all I did was change 3 distances.

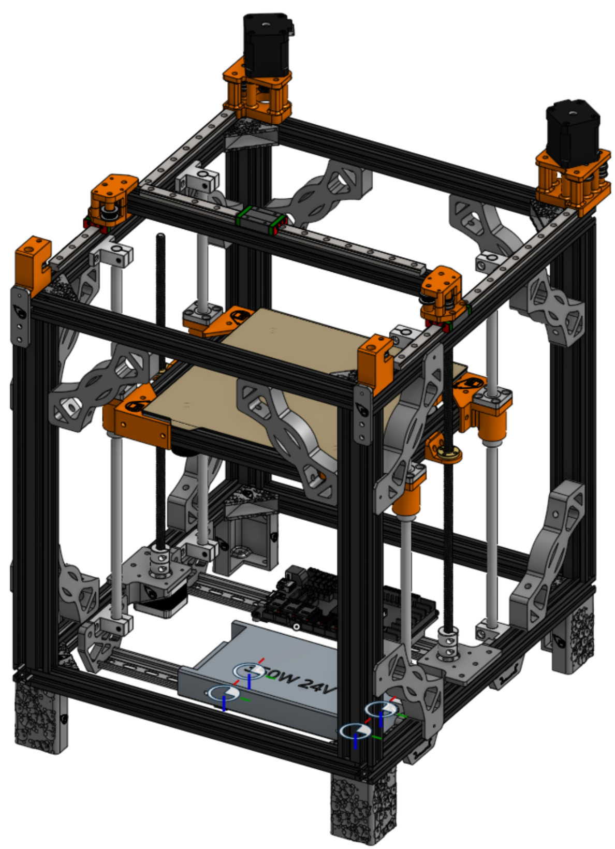
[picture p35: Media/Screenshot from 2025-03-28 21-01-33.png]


[Onshape Link](https://cad.onshape.com/documents/1de0655c0501c319c0be82e5/w/00a76129439a8316e13df1dd/m/aa6b344d97396a3ec29ddd6a/e/f03e8779d1a8cc2741025c01)

I also had ideas for bed changing mechanisms

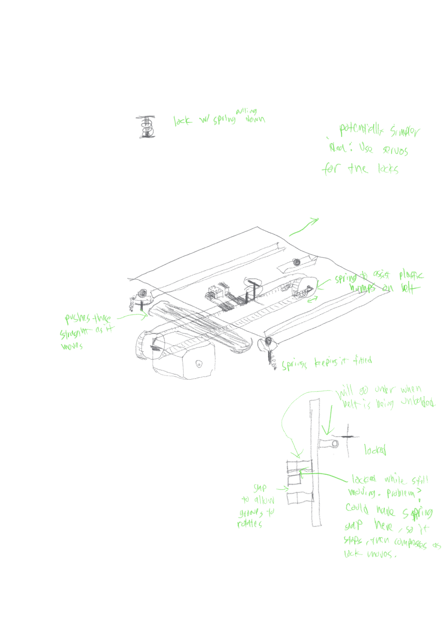
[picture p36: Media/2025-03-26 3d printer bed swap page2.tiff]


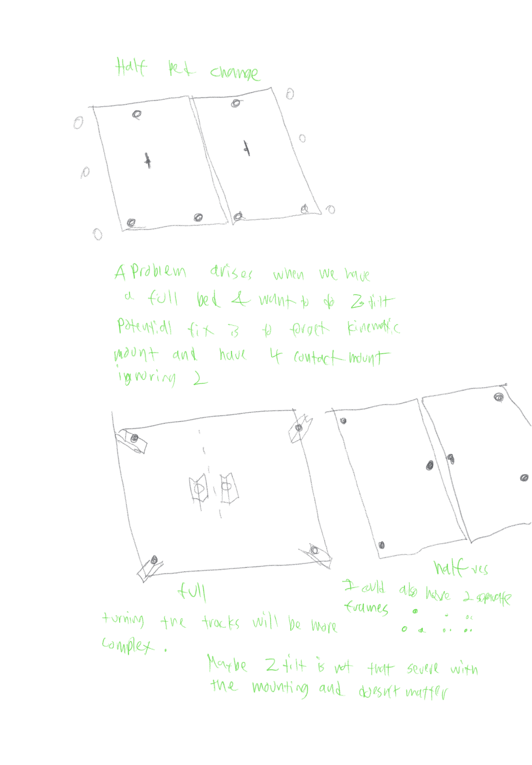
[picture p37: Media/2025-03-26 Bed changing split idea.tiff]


Time 8 hrs

## Finished X axis - March 27th, 2025

X axis is finished! (doesn't include toolhead)
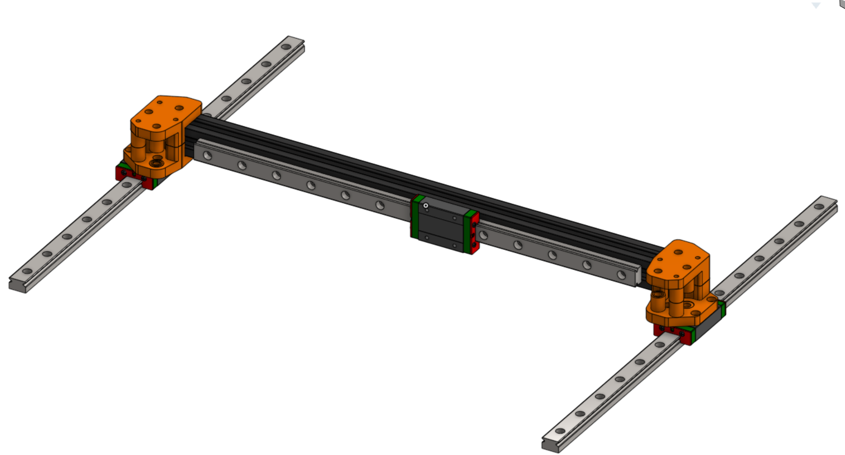
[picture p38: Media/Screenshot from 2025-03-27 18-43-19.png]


I also changed the pockmark size on the base standoffs, to make the design bigger.

I added all my base and accent colors to this now, spicing it up. Stationary parts are Grey, moving parts are Orange.

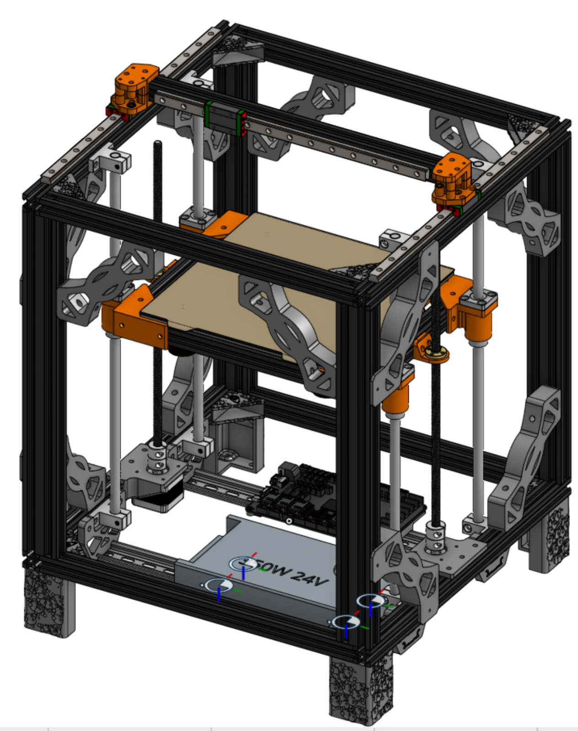
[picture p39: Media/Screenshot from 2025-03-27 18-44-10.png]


[Onshape Link](https://cad.onshape.com/documents/1de0655c0501c319c0be82e5/w/00a76129439a8316e13df1dd/m/6000dfeccf72bd922665b3dd/e/abe2e35d4e7a15af75f9cffc)

Time: 4 hrs

## Started on X beam March 25th, 2025

Didn't take any pictures, but I am mostly finished with the x joints

Time: 2hrs

## Add Electronics base - March 24th, 2025

I changed the bite marks on the corner peices to an actual meteor texture that I made. I will put that texture on all non-critical parts now to spice things up!
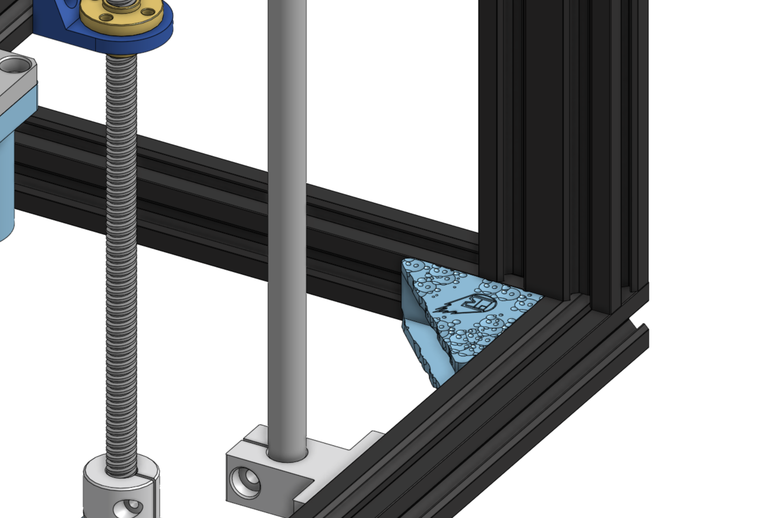
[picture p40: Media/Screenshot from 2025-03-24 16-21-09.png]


I also spent some time designing the bottom electronics enclosure parts.

I also spent 2 hours researching using USB for all peripherial devices instead of CANbus, and it seems like it has a lot more potential without much downside. CAN bus is better for redundancy and long distance, which is not really used for 3D printers. It also ends up being a drag for toolchangers with hotswap, and for high throughput data required by cameras. I just need to use USB over a sheilded cable, and have a hub! The LDO Nitehawk SB boards look pretty cool, with that special molex connector with big power lines and small datalines. I could design a hub for that connector! Similar to [birds nest](https://store.isiks.tech/products/birds-nest) but cheaper and with USB-c.

My printer is really shaping up! I have all of the base designed and assembled. I now only need the top motion, toolchanging toolhead, and possible enclosure! I've reached the point where I now consider it prudent to include a main step file in the repo, with half the mechanical design finished.
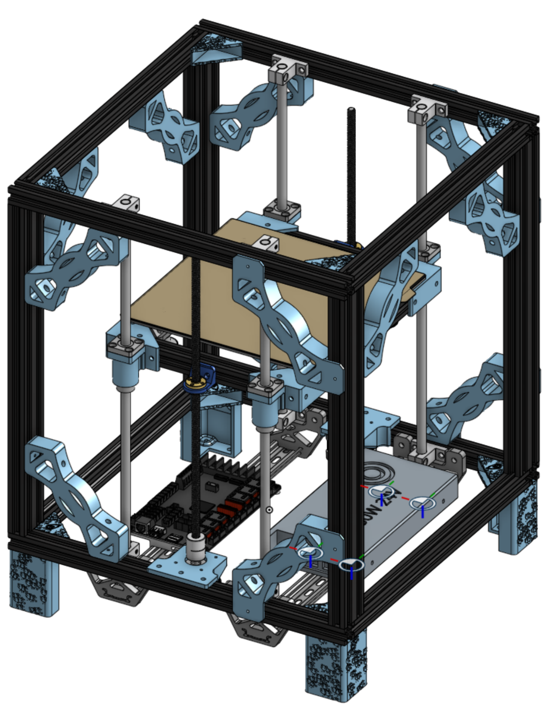
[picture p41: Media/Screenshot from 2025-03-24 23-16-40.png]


[Onshape link](https://cad.onshape.com/documents/1de0655c0501c319c0be82e5/w/00a76129439a8316e13df1dd/m/631436aa15fda19fa4fe5d01/e/f03e8779d1a8cc2741025c01)

Time: 8 hrs

## Finished bed frame - March 23rd, 2025

I have attached all the parts and knobs and stuff, and added some motion capability.

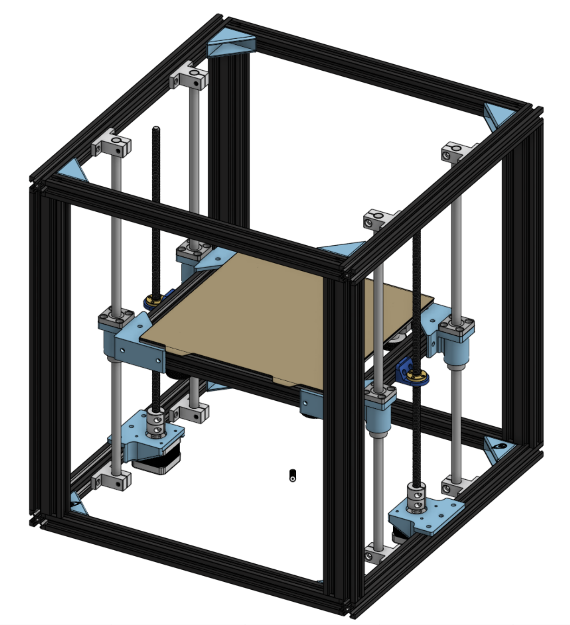
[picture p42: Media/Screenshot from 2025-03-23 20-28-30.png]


I also add fun bite marks to some the pieces, in imitation of a meteor.

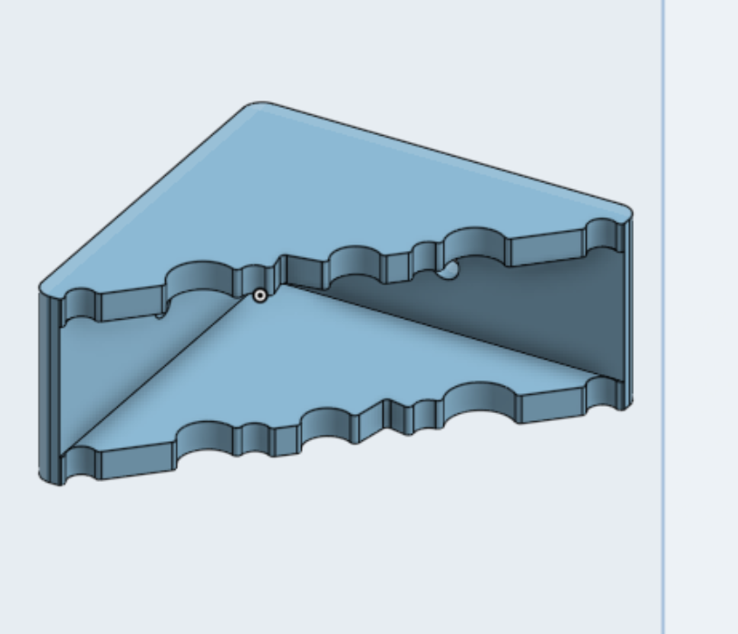
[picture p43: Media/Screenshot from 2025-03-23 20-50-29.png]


[Onshape Link](https://cad.onshape.com/documents/1de0655c0501c319c0be82e5/w/00a76129439a8316e13df1dd/m/680a472921ba0d3f7ccb1c2f/e/5ef495c38173f41e0befecf5)

Time: 2hrs

## Updated Icon - March 22nd, 2025
I changed the design a bit to emphasize the M dip and make it look somewhat more like a toolhead.



Time: 1hr

## Started bed frame design - March 18th, 2025
I created a combined bed corner and z linear rail peice. I hope it is rigid enough!

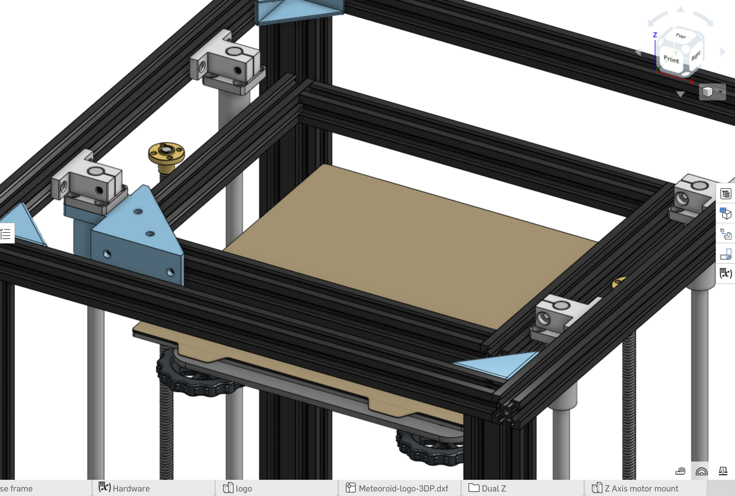
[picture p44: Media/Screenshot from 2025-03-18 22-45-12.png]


[Onshape Link](https://cad.onshape.com/documents/1de0655c0501c319c0be82e5/w/00a76129439a8316e13df1dd/m/f90ea5979eb5aaab7db21657/e/5ef495c38173f41e0befecf5)

Time: 1hr

## Added Z axis rails - March 17th, 2025
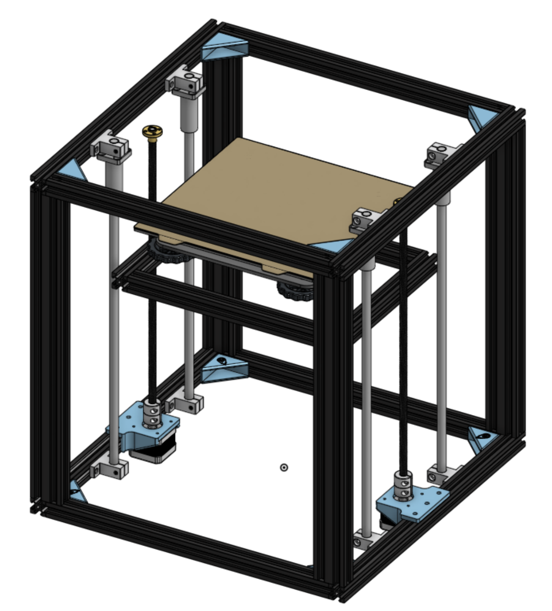
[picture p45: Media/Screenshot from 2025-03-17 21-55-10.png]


[Onshape Link](https://cad.onshape.com/documents/1de0655c0501c319c0be82e5/w/00a76129439a8316e13df1dd/m/ac507458f413c697b0cd875a/e/5ef495c38173f41e0befecf5)

Time: 1hr

## Started frame stiffener - March 9th, 2025

I designed a fun frame stiffener peice
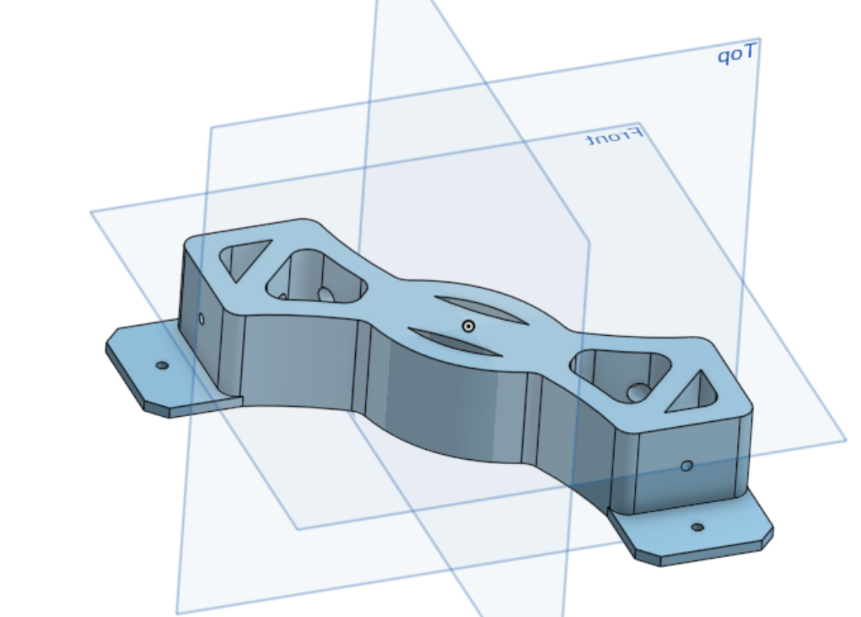
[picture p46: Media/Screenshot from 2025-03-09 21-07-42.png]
Frame Stiffener


[Onshape Link](https://cad.onshape.com/documents/1de0655c0501c319c0be82e5/w/00a76129439a8316e13df1dd/m/2ae4412215810c69bc8e58e2/e/1f99f85a2999227fc57382c6)

Time: 2 hr

## Finished Logo digital design - March 8th, 2025

I spent quite a few hours working on turning my drawings into a logo for my printer. I created multiple versions of it for different situations and for 3D.

Final logo:
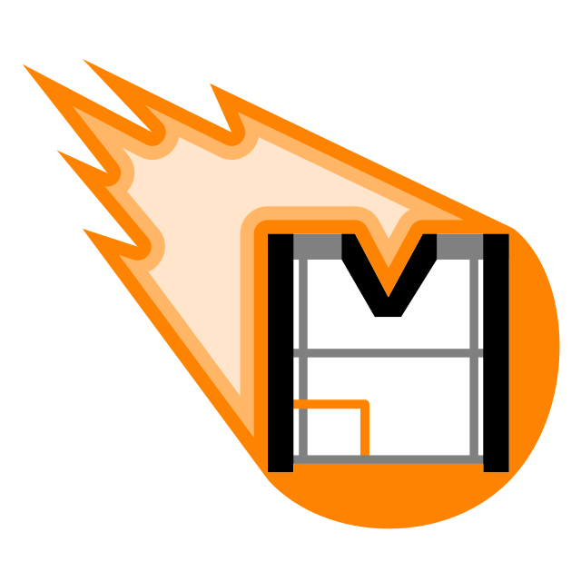
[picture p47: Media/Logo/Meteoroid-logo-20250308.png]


### My Process for creating Logo types
1. Create the base color logo. Use offset live path effect with rounded corners and then flatten it to a normal object for the internal light colors. More control than the Path Outset tool. Break it apart and delete the weird extra small shapes. Make sure to name all objects, and have a layer for the printer and layer for the burn
2. Copy and start on two-tone version. Delete the 3rd inset color. Make sure the color pallet only has Primary and Background colors. Change all lines to Primary color, and make sure everything else is a fill color. Re-create the burn internal offset except without internal edges. The burn has to go behind the printer now.
3. Copy and start on black and white version. Only change necessary, which should just be the colors
4. For Mono, take the path difference of the trail and the the background so that you have no background fill object. Delete the fill object for the printer. Now it should be transparent and have only one color
5. Finally, to get a logo that can be extruded in 3D, convert all strokes to paths, boolean union on all paths, Get ride of all groups and layers, and save as a DXF R14 file without changing any of the defaults. 

Time: 6 hrs

## Base Frame - March 5th, 2025

Finished base Frame today, I just need to add stiffeners
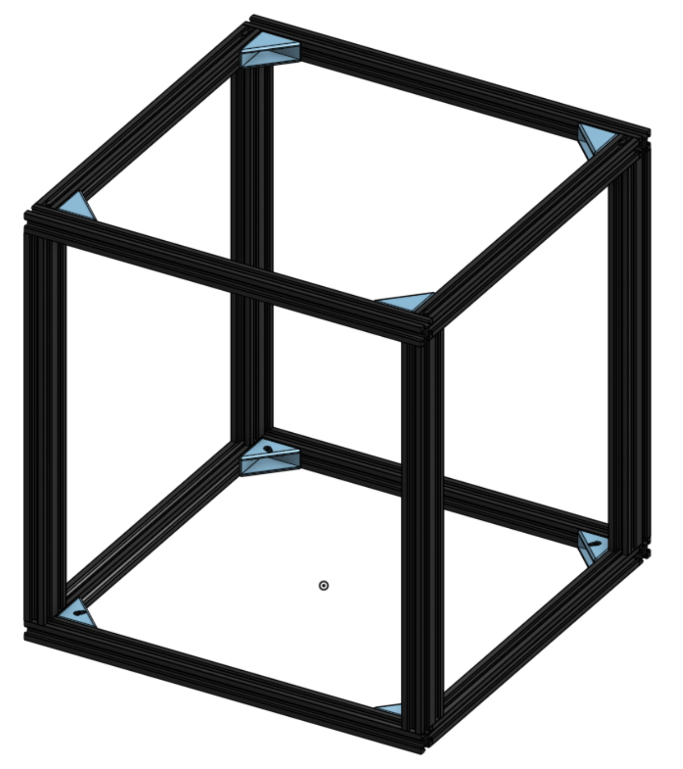
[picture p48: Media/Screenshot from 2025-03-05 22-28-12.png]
Base Frame


[Onshape Link](https://cad.onshape.com/documents/1de0655c0501c319c0be82e5/w/00a76129439a8316e13df1dd/m/cbfba813138ca8a3b26123b0/e/76ac3e39a1abc7fd322101c5)

Time: 30 min

## Logo ideas - March 1st, 2025
Some logo ideas


Time : 30min

## Back at it - Feb 25, 2025
Okay, I'm back at it today, starting actual design work! I took my time creating a configerable vslot beam part that can change to any length on demand. I also assembled the base rectangle for the bottom.
base square

[Onshape Link](https://cad.onshape.com/documents/1de0655c0501c319c0be82e5/w/00a76129439a8316e13df1dd/m/b323f8763260d1f753c2db33/e/71c7bdc91eebbb5c66aa9fbc)

Time: 1 hr

## More ideas - Feb 4th, 2025

I decided that for rails I should instead go with West3D Berserker MGN12 rails, they high quality and from my favorite supplier

I had a greate idea for a bed ejection and combo scraper system for my printer using one motor. Basically it is a belt drive that at one end pulls the scrapper across the bed towards the front, but if it reverses it disengages and springs back, starting to push the bed out towards the back. There would be a robot port at the back to handle the bed and transport it to storage somehow.

Bed Options:
- 3d Printer bed, G10
- Laser bed with metal heat fins
- CNC Steel bed
- Pick & Place bed with a camera and part alignment jigs

There are also additional slots for toolhead accessories around the top of the printer that would have to be swapped automatically. I'm not sure the best way to replace accessory bays with an automated robot, since its difficult to reach inside the printer. 

Accessory bay options:
- Nozzles for PnP head
- Feeders for PnP
- Klicky Probe
- Waste Material Ejection for color change and cleaning
- Revo hotends
- Camera mount

For the toolhead there are 4 slots for different *active* heads, but many more toolheads will likely be used, and I want them automatically loaded by some robot from storage. I'm thinking of having an extension arm that locks and grabs the toolheads the same way the printer carraige would (in towards the printer), but it would then drop down, go under the frame beam, and be encapsulated into a driving robot to take it to storage.

These robots would be completely independent of the manufacturing machines, they are driving robots with mechanum or swerve base capabily of transporting parts to storage or between machines easily. These carry Heads, Beds, Accessory Bays, Input Material, Output Material, and whatever else I decide should be automatically changed on the fly.

The head and bed should have 2 communication lanes and 2 high power lanes to have maximum flexiblity (if I wanted cameras on the parts for example). It is assumed that CAN bus and or USB 3 are used for high reliability.

Time: 30 min

## Cont. Part Research - Feb 3rd, 2025

I added a few parts to my list.
First up is the motherboard. I will still be reusing the BTT Octopus Pro for the printer, but for the BOM I decided to switch from the SKR mini E3 to a SKR Pico, which is a cheaper option that provides virtually the same functionality.

Since this is a modular industrial 3D printer, I will be having a tool changer with 4 slots. Without the Octopus I have, this would be impossible on normal motherboards. Even using the big motherboard, I would have big problem routing cables for many different toolheads. My best choice is to have a toolhead board that simplifies wiring, and for this I want the BTT EBB 36

I have also decided on the motors: LDO Motors 42STH48-2804AH. These are part of the Super Speedy lineup, and are high temp, high current 1.8 degree motors.

For the motion system I want to use 350mm Mitsumi Linear rails (3 of them) top mounted, and Gate belts

Additions:
- Motherboard on BOM: BTT SKR Pico
- Klipper Host: RPI zero 2 w or a spare SBC I have
- Toolboard: BTT EBB 36
- Carraige CoreXY Motors: LDO 42STH48-2804AH(S55)

Time: 1hr

## Part Research - Feb 2nd, 2025

Today I spent several hours researching parts for my 3D printer that would deliver high performance and fit relatively in budget. I am planning on tearing down a CoreXY printer I already own and redesign from scratch. Some of the parts like the Ender 5 frame can be reused, so the price can be lowered for my prototype. I will still include the total cost with every part I have used, but the price I pay will be lower.

I new right away that the hotend had to have no compromises, so I started looking at hotend similar to the Rapido. I ended up finding the Triangle Labs Rapido ACE, which appears to be the newest and best in the rapido clone lineup. I also considered other hotends like a Bambu Lab or clone. The bambu lab hotends are nice and cheap, but I think they are limited for *super* high speed printing. They are also proprietary. I spent awhile pondering the Phaetus Dragon UHF hotend for awhile, another popular choice. I decided that it was a decent option, but the Rapido hotend had the highest capability. This took most of my research time

For the extruder I am going to go with something I know is stable and strong, the LDO Orbitor 2.0 extruder. This has been running on one of my printer much more reliably than the previous sherpa mini, and I haven't found another extruder that balances price and extrusion force and weight so well.

I also briefly considered Smart Orbiter 3.0 all in one due to the lower price, but this didn't have a super good hotend.

For controlling I know I need something cheap that can support klipper and has TMC drivers. The community disposition seemed to be towards the BigTreeTech E3 v3, so I threw it in without much consideration. The BOM will include this, but in reality I will be reusing a BTT Octopus Pro motherboard from the old printer build, it is super nice and I don't want it to go to waste

I want to use some quality stepper motors, so I will use LDO motors for the carraige, and some cheap motors for the Z- axis

Summary:
- Hotend: Triangle Labs Rapido ACE
- Extruder: LDO Orbiter 2.0 with 36mm pancake motor
- Motherboard: BTT SKR mini E3 (my build will use BTT Octopus Pro)
- 2 Nema 17 motors from LDO 42STH48-something
- 2 nema 17 Ender 3 z-axis motors

Time: 4 hrs

## Concept - Feb 1st, 2025
The basic concept is this: A desktop machine with plug and play heads and beds. Chain these together and add robot carriages in between and you got yourself an awesome factory that can fit in a bench. This is an opensource project. The cost of the _entire system_ will likely be several thousand dollars, with the main machine limited to $300 budget. I aim to lower the cost of a complete industrial system as much as possible.

The head and bed have 2 communication lanes and 2 high power lanes. It is assumed that CAN bus and or USB 3 are used for high reliability.

Time: 30 min

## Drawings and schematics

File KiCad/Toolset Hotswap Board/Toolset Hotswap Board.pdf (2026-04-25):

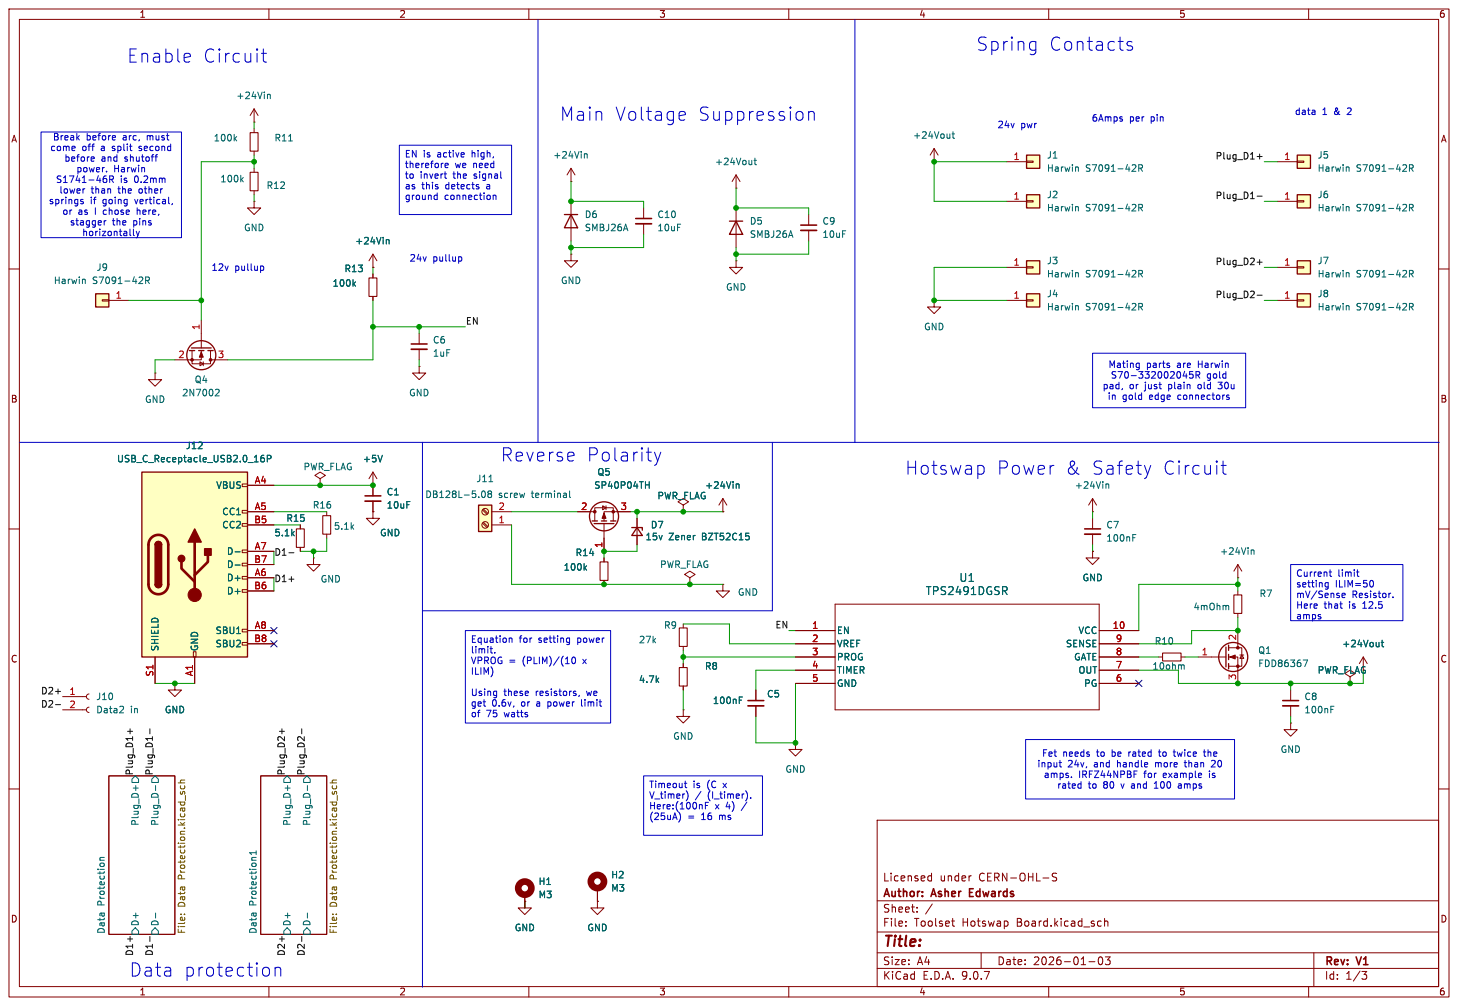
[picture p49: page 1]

Break before arc, must come off a split second
Plug_D1+ D2+

EN is active high,
to invert the signal as this detects a

lower than the other springs if going vertical, or as I chose here, stagger the pins

pad, or just plain old 30u

Hotswap Power & Safety Circuit Reverse Polarity

Equation for setting power

input 24v, and handle more than 20
amps. IRFZ44NPBF for example is
rated to 80 v and 100 amps

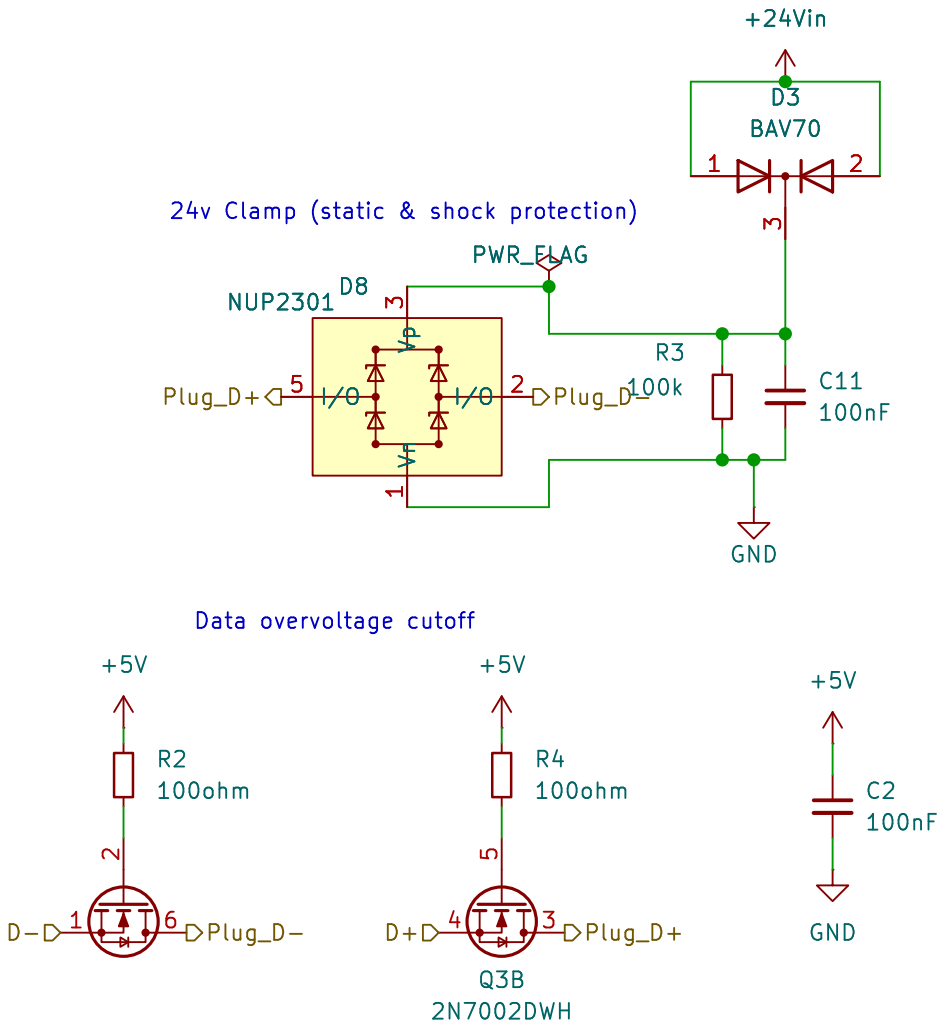
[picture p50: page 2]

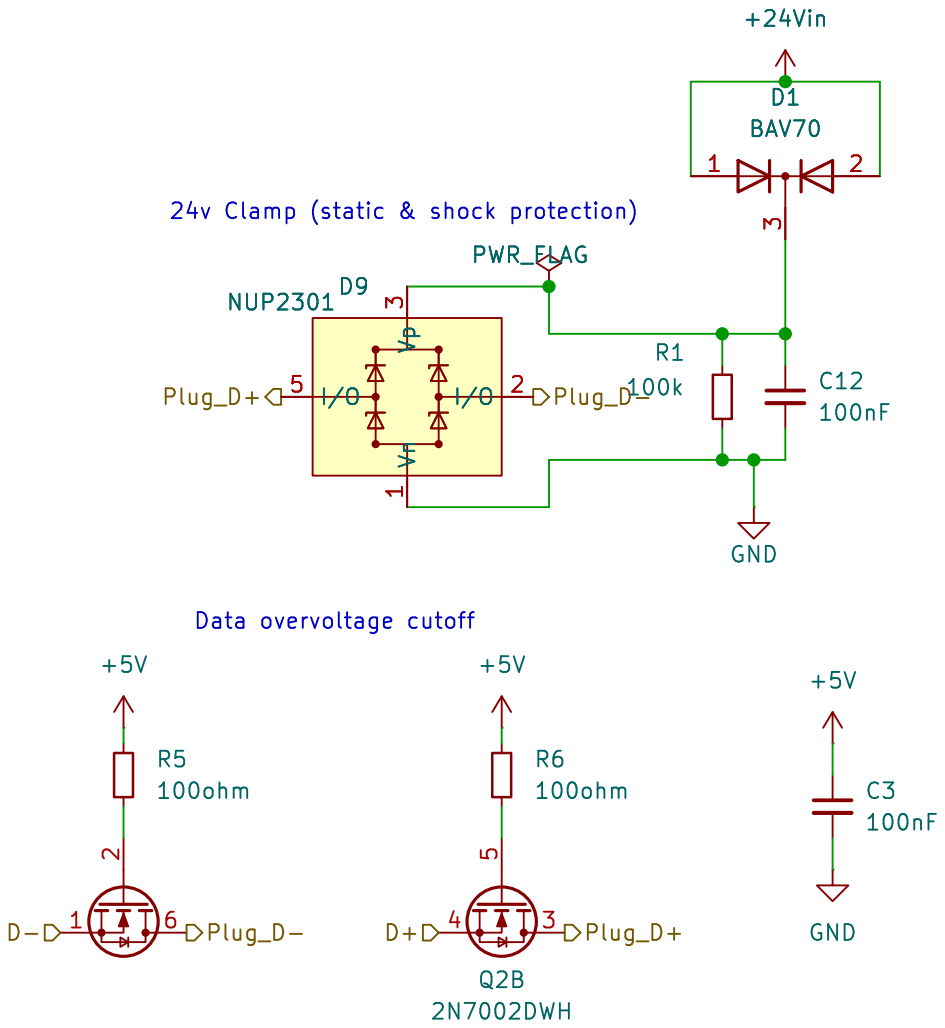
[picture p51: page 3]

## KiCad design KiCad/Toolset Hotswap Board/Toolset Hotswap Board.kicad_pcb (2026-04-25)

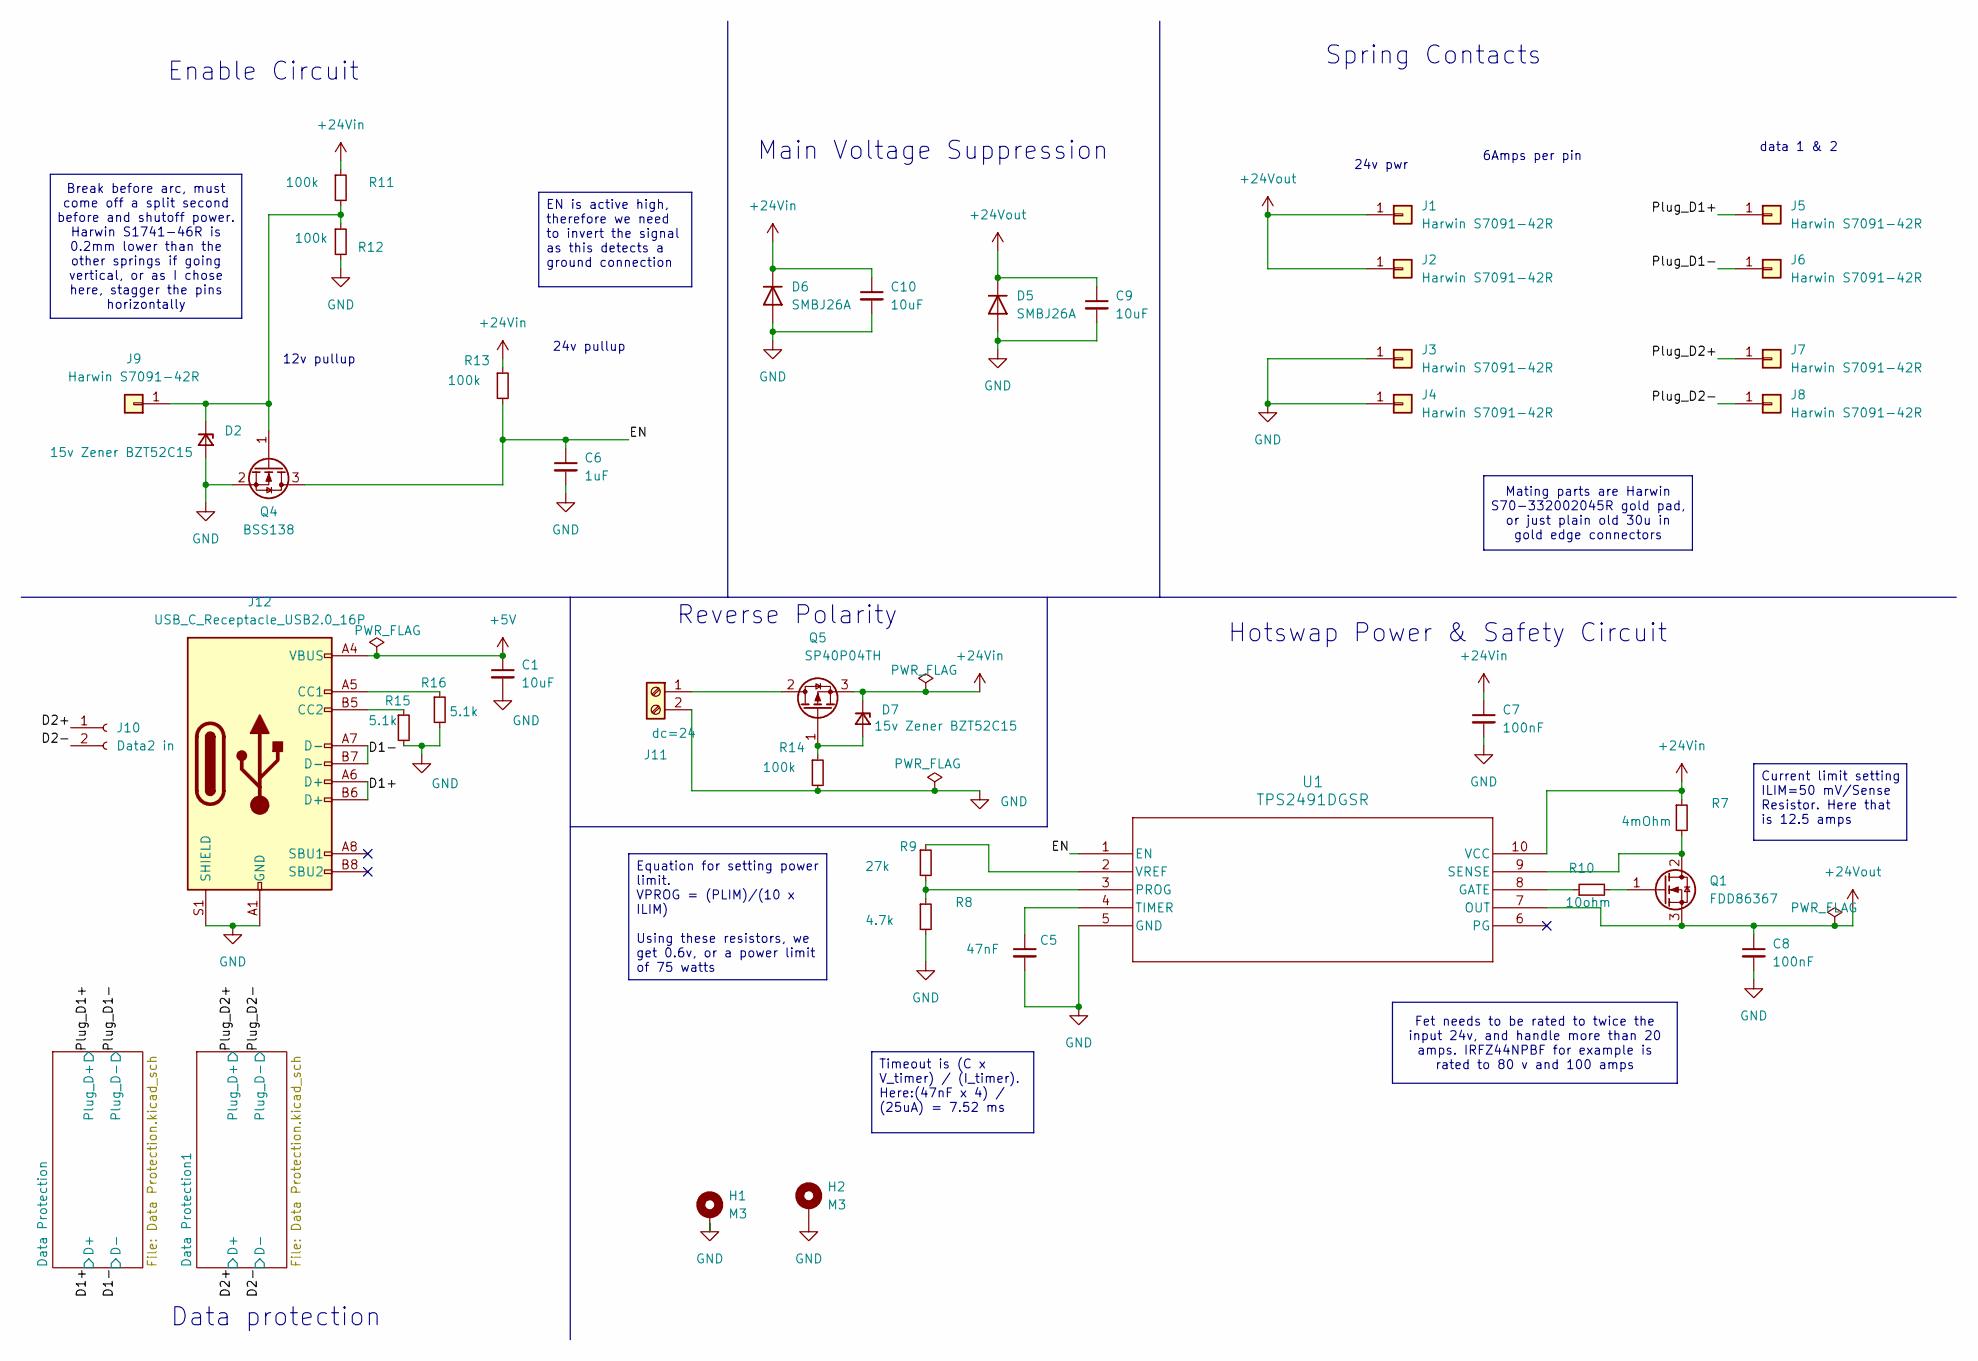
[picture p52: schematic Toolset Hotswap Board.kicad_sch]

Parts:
C1, C9, C10: 10uF; C_0805_2012Metric; LCSC C440198
C5: 47nF; C_0603_1608Metric; LCSC C1622
C6: 1uF; C_0603_1608Metric; LCSC C15849
C7, C8: 100nF; C_0402_1005Metric; LCSC C307331
D2, D7: 15v Zener BZT52C15; D_SOD-123; LCSC C2932746
D5, D6: SMBJ26A; D_SMB; LCSC C123820
H1, H2: M3; MountingHole_3.2mm_M3_Pad_Via
J1, J2, J3, J4, J5, J6, J7, J8, J9: Harwin S7091-42R; HARWIN_S7091-42R; LCSC C21394879
J10: Data2 in; PinSocket_1x02_P2.54mm_Vertical
J11: dc=24; TerminalBlock_CUI_TB007-508-02_1x02_P5.08mm_Horizontal; LCSC C430601
J12: USB_C_Receptacle_USB2.0_16P; USB_C_Receptacle_G-Switch_GT-USB-7010ASV; LCSC C2988369
Q1: FDD86367; TO-252-2; LCSC C903589
Q4: BSS138; SOT-23; LCSC C7420339
Q5: SP40P04TH; TO-252-2; LCSC C41355036
R7: 4mOhm; R_2512_6332Metric; LCSC C7420003
R8: 4.7k; R_0402_1005Metric; LCSC C25900
R9: 27k; R_0402_1005Metric; LCSC C25771
R10: 10ohm; R_0402_1005Metric; LCSC C25077
R11, R12, R13, R14: 100k; R_0402_1005Metric; LCSC C25741
R15, R16: 5.1k; R_0402_1005Metric; LCSC C25905
U1: TPS2491DGSR; VSSOP-10_3x3mm_P0.5mm; LCSC C273636

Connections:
+5V: C1.1, J12.A4 (VBUS), J12.A9 (VBUS), J12.B4 (VBUS), J12.B9 (VBUS); also elsewhere on the board
+24Vin: C7.1, C10.1, D6.1 (K), D7.1 (K), Q5.3 (S), R7.1, R11.1, R13.1, U1.10 (VCC); also elsewhere on the board
+24Vout: C8.1, C9.1, D5.1 (K), J1.1, J2.1, Q1.3 (S), U1.7 (OUT)
/D1+: J12.A6 (D+), J12.B6 (D+); also elsewhere on the board
/D1-: J12.A7 (D-), J12.B7 (D-); also elsewhere on the board
/D2+: J10.1; also elsewhere on the board
/D2-: J10.2; also elsewhere on the board
/EN: C6.1, Q4.3 (D), R13.2, U1.1 (EN)
/Plug_D1+: J5.1; also elsewhere on the board
/Plug_D1-: J6.1; also elsewhere on the board
/Plug_D2+: J7.1; also elsewhere on the board
/Plug_D2-: J8.1; also elsewhere on the board
GND: C1.2, C5.2, C6.2, C7.2, C8.2, C9.2, C10.2, D2.2 (A), D5.2 (A), D6.2 (A), H1.1, H2.1, J3.1, J4.1, J11.2, J12.A1 (GND), J12.A12 (GND), J12.B1 (GND), J12.B12 (GND), J12.S1 (SHIELD), Q4.2 (S), R8.2, R12.2, R14.2, R15.2, R16.2, U1.5 (GND); also elsewhere on the board
unnamed: D2.1 (K), J9.1, Q4.1 (G), R11.2, R12.1
unnamed: D7.2 (A), Q5.1 (G), R14.1
unnamed: J11.1, Q5.2 (D)
unnamed: J12.A5 (CC1), R16.1
unnamed: J12.B5 (CC2), R15.1
unnamed: Q1.2 (D), R7.2, U1.9 (SENSE)
unnamed: Q1.1 (G), R10.2
unnamed: R10.1, U1.8 (GATE)
unnamed: R8.1, R9.2, U1.3 (PROG)
unnamed: C5.1, U1.4 (TIMER)
unnamed: R9.1, U1.2 (VREF)

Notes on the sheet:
Enable Circuit
Main Voltage Suppression
data 1 & 2
24v pwr
Spring Contacts
6Amps per pin
Reverse Polarity
Data protection
24v pullup
Hotswap Power & Safety Circuit
12v pullup
Mating parts are Harwin S70-332002045R gold pad, or just plain old 30u in gold edge connectors
EN is active high, therefore we need to invert the signal as this detects a ground connection
Current limit setting ILIM=50 mV/Sense Resistor. Here that is 12.5 amps
Fet needs to be rated to twice the input 24v, and handle more than 20 amps. IRFZ44NPBF for example is rated to 80 v and 100 amps
Timeout is (C x V_timer) / (I_timer). Here:(47nF x 4) / (25uA) = 7.52 ms
Break before arc, must come off a split second before and shutoff power. Harwin S1741-46R is 0.2mm lower than the other springs if going vertical, or as I chose here, stagger the pins horizontally
Equation for setting power limit. VPROG = (PLIM)/(10 x ILIM) Using these resistors, we get 0.6v, or a power limit of 75 watts

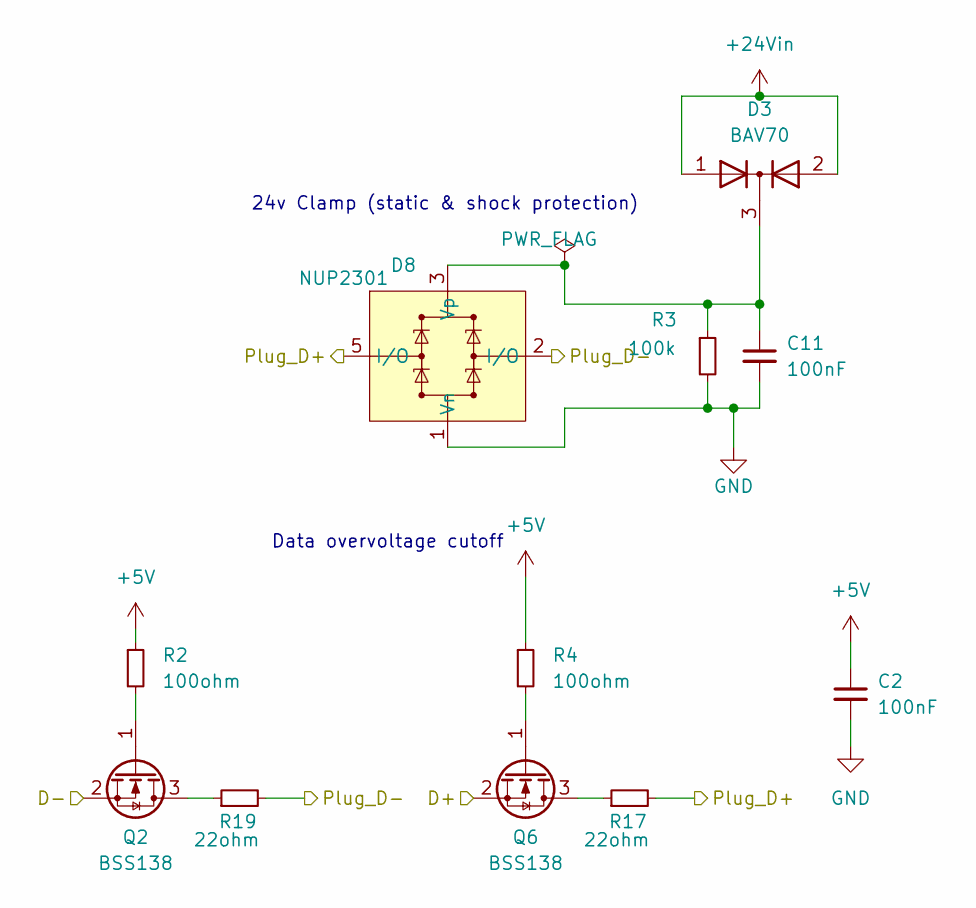
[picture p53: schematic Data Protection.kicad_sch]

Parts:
C2, C11: 100nF; C_0402_1005Metric; LCSC C307331
D3: BAV70; SOT-23; LCSC C68978
D8: NUP2301; SOT-363_SC-70-6; LCSC C708740
Q2, Q6: BSS138; SOT-23; LCSC C7420339
R2, R4: 100ohm; R_0402_1005Metric; LCSC C25076
R3: 100k; R_0402_1005Metric; LCSC C25741
R17, R19: 22ohm; R_0402_1005Metric; LCSC C25092

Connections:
+5V: C2.1, R2.1, R4.1; also elsewhere on the board
+24Vin: D3.1 (A), D3.2 (A); also elsewhere on the board
/D1+: Q6.2 (S); also elsewhere on the board
/D1-: Q2.2 (S); also elsewhere on the board
/Plug_D1+: D8.5 (I/O), R17.2; also elsewhere on the board
/Plug_D1-: D8.2 (I/O), R19.2; also elsewhere on the board
GND: C2.2, C11.2, D8.1 (Vn), R3.2; also elsewhere on the board
unnamed: C11.1, D3.3 (K), D8.3 (Vp), R3.1
unnamed: Q2.3 (D), R19.1
unnamed: Q2.1 (G), R2.2
unnamed: Q6.3 (D), R17.1
unnamed: Q6.1 (G), R4.2

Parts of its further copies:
C3, C12: 100nF; C_0402_1005Metric; LCSC C307331
D1: BAV70; SOT-23; LCSC C68978
D9: NUP2301; SOT-363_SC-70-6; LCSC C708740
Q3, Q7: BSS138; SOT-23; LCSC C7420339
R1: 100k; R_0402_1005Metric; LCSC C25741
R5, R6: 100ohm; R_0402_1005Metric; LCSC C25076
R18, R20: 22ohm; R_0402_1005Metric; LCSC C25092

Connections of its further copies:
+5V: C3.1, R5.1, R6.1; also elsewhere on the board
+24Vin: D1.1 (A), D1.2 (A); also elsewhere on the board
/D2+: Q7.2 (S); also elsewhere on the board
/D2-: Q3.2 (S); also elsewhere on the board
/Plug_D2+: D9.5 (I/O), R18.2; also elsewhere on the board
/Plug_D2-: D9.2 (I/O), R20.2; also elsewhere on the board
GND: C3.2, C12.2, D9.1 (Vn), R1.2; also elsewhere on the board
unnamed: C12.1, D1.3 (K), D9.3 (Vp), R1.1
unnamed: Q3.3 (D), R20.1
unnamed: Q3.1 (G), R5.2
unnamed: Q7.3 (D), R18.1
unnamed: Q7.1 (G), R6.2

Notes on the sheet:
Data overvoltage cutoff
24v Clamp (static & shock protection)

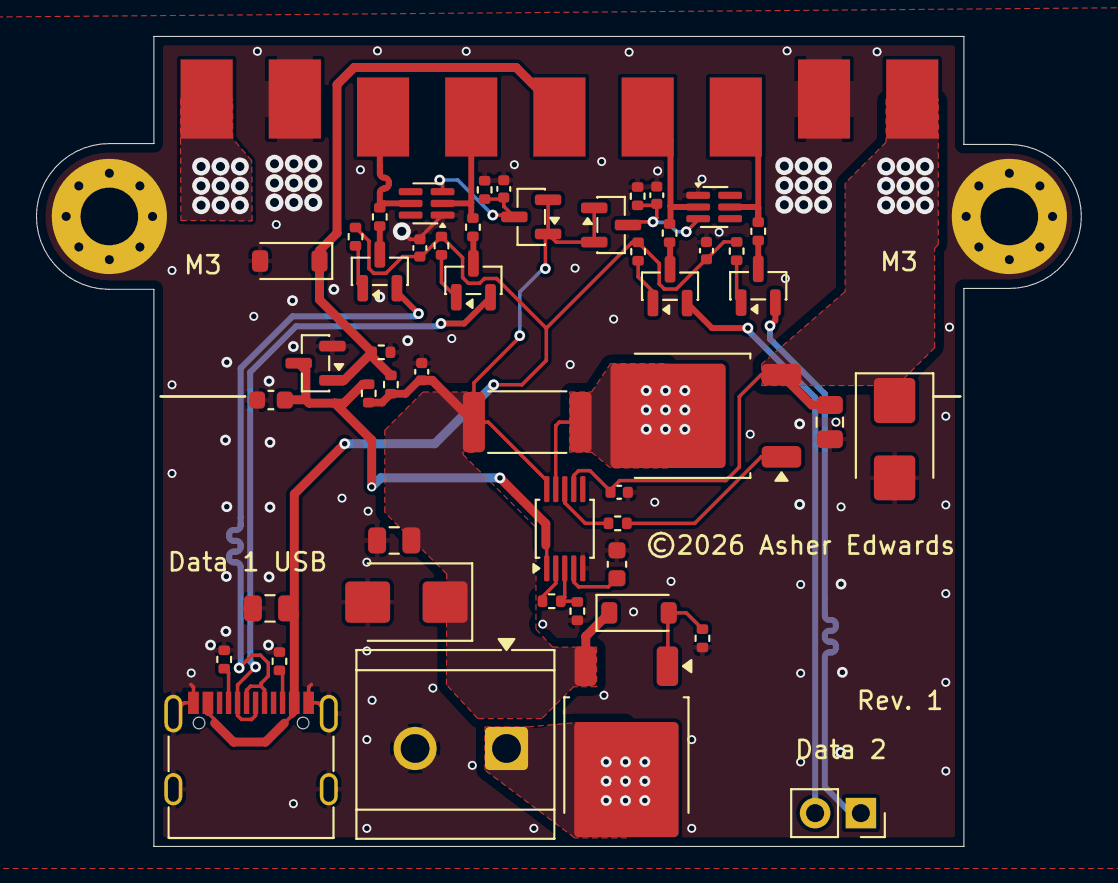
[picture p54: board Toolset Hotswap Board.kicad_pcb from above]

Board: 2 copper layers, 58.0 x 45.0 mm, 61 parts (0 on the bottom side), 34 nets.

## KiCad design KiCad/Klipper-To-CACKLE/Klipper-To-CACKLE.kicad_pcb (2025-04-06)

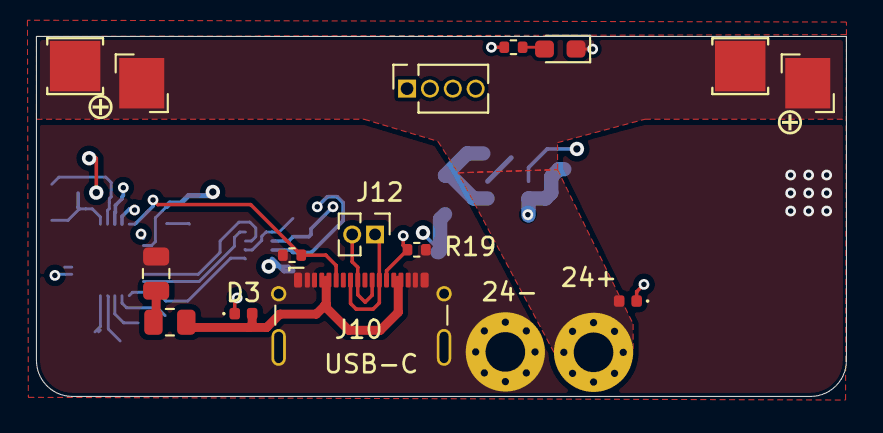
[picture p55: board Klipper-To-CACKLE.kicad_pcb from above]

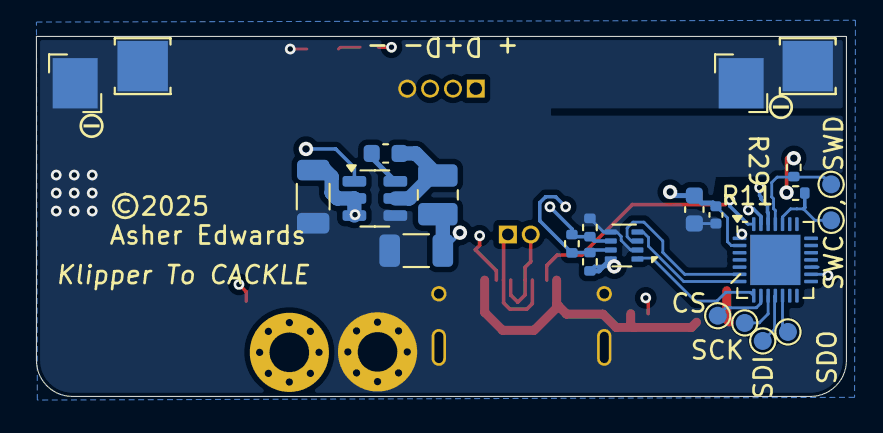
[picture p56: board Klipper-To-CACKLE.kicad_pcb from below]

Board: 4 copper layers, 45.0 x 20.0 mm, 41 parts (25 on the bottom side), 25 nets.

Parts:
C7: 10uF, 16v; C_0805_2012Metric
C25: 100nF, 16v; C_0402_1005Metric
C26: 4.7uF, 16v; C_0603_1608Metric
C27: 22uf, 16v CL31A226MOCLNN; C_1206_3216Metric
C28: 22uf, 32v; C_1206_3216Metric
C40: 100nF, 16v; C_0603_1608Metric
D2, D3: GSDH3005; D_0402_1005Metric
D4: 2.6~3.1 Fv Green 5ma; LED_0603_1608Metric_Pad1.05x0.95mm_HandSolder
H1: HIGHPWR; MountingHole_2.2mm_M2_Pad_Via
H2: HIGHGND; MountingHole_2.2mm_M2_Pad_Via
J1, J3, J6, J7: Keystone 3579; Keystone_3579
J4, J5, J8, J9: Keystone 3569; Keystone_3569_half
J10: G-Switch-GT-USB-7025; USB_C_G-Switch_GT-USB-7025-JLCPCBv
J11: 1.27mm 4 pin socket; PinSocket_1x04_P1.27mm_Vertical
J12: USB; PinHeader_1x02_P1.27mm_Vertical
L3: 2.2uH, WIP322512A-2R2MLDG; L_1008_2520Metric
R2: 2ohm; R_0805_2012Metric
R11, R29: 10k; R_0402_1005Metric
R19, R33: 5.1k; R_0402_1005Metric
R25: 80.6 ohm; R_0402_1005Metric
R26, R27, R28: 120 ohm; R_0402_1005Metric
TP1: SWC; TestPoint_Pad_D1.0mm
TP2: CS; TestPoint_Pad_D1.0mm
TP3: SCK; TestPoint_Pad_D1.0mm
TP4: SWD; TestPoint_Pad_D1.0mm
TP5: SDI; TestPoint_Pad_D1.0mm
TP6: SDO; TestPoint_Pad_D1.0mm
U2: AP63203WU; TSOT-23-6
U5: THVD1420DRLR; SOT-583-8
U6: CH32X035G8U6; QFN-28-1EP_4x4mm_P0.4mm_EP2.8x2.8mm

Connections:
/Connectors/3.3v: C25.1, C26.1, C27.1, J11.1, L3.2, R11.2, R28.1, R29.2, U2.1 (FB), U5.8 (VCC), U6.2 (VDD)
/Connectors/CC1: J10.A5 (CC1), R33.2, U6.28 (CC1/PC14)
/Connectors/CC2: J10.B5 (CC2), R19.2, U6.1 (CC2/PC15)
/Connectors/D+: J10.A6 (D+), J10.B6 (D+), J12.1, U6.27 (USB1_DP/PC17)
/Connectors/D-: J10.A7 (D-), J10.B7 (D-), J12.2, U6.26 (USB1_DM/PC16)
/Connectors/HIGHPWR: D2.2 (A), H1.1, J1.1, J3.1, J4.1, J5.1
/Connectors/RS485+: J11.2, R27.2, R28.2, U5.7 (B)
/Connectors/RS485-: J11.3, R26.1, R27.1, U5.6 (A)
/Connectors/USBPWR: D3.2 (A), J10.A4 (VBUS), J10.A9 (VBUS), J10.B4 (VBUS), J10.B9 (VBUS), R2.2
/MCU/CS: TP2.1, U6.9 (ADC4/PA4)
/MCU/LED: R25.1, U6.16 (PB1/PB5/ADC9)
/MCU/MISO: TP5.1, U6.11 (ADC6/PA6)
/MCU/MOSI: TP6.1, U6.12 (ADC7/PA7)
/MCU/SCLK: TP3.1, U6.10 (ADC5/PA5)
/MCU/UART1-RTS: U5.3 (DE), U6.6 (ADC1/PA1)
/MCU/UART1_RX: U5.1 (RO), U6.8 (ADC3/PA3)
/MCU/UART1_TX: U5.4 (DI), U6.7 (ADC2/PA2)
/PSU/Always On PWR: C28.1, D2.1 (K), D3.1 (K), U2.2 (EN), U2.3 (IN)
/SCL: R11.1, TP1.1, U6.24 (SWCLK/PC19)
/SDA: R29.1, TP4.1, U6.25 (SWDIO/PC18)
GND: C7.2, C25.2, C26.2, C27.2, C28.2, D4.1 (K), H2.1, J6.1, J7.1, J8.1, J9.1, J10.A1 (GND), J10.A12 (GND), J10.B1 (GND), J10.B12 (GND), J10.GND, J10.S1 (SHIELD), J11.4, R19.1, R26.2, R33.1, U2.4 (GND), U5.2 (~RE), U5.5 (GND), U6.29 (GND)
unnamed: C7.1, R2.1
unnamed: D4.2 (A), R25.2
unnamed: C40.1, U2.6 (BST)
unnamed: C40.2, L3.1, U2.5 (SW)

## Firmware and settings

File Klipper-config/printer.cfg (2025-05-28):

# This file contains common pin mappings for the BigTreeTech Octopus
# Pro v1.0 board.

# Important! Do not use this config with an Octopus Pro v1.1 board as
# doing so could result in a heater being inadvertently enabled.

# To use this config, start by identifying the micro-controller on the
# board - it is an STM32F446ZET6 for my board.  Select
# the appropriate micro-controller in "make menuconfig" and select
# "Enable low-level configuration options". For STM32F446 boards the
# firmware should be compiled with a "32KiB bootloader" and a "12MHz
# crystal" clock reference. For STM32F429 boards use a "32KiB
# bootloader" and an "8MHz crystal". For STM32H723 boards use a
# "128KiB bootloader" and a "25Mhz crystal".

# See docs/Config_Reference.md for a description of parameters.

# Note: Modified for my use

[include mainsail.cfg]
[include probe_and_bed_mesh.cfg]
[include advanced_tuning.cfg]
[include macros.cfg]
[include sounds.cfg]
[include pause_custom.cfg]

[danger_options]
temp_ignore_limits: True

# Driver0
# A motor
[stepper_y]
step_pin: PF13
dir_pin: !PF12
enable_pin: !PF14
microsteps: 32
rotation_distance: 40
full_steps_per_rotation:200
position_endstop: 0
position_max: 150
position_min: 0
homing_speed: 20
endstop_pin: tmc2209_stepper_y:virtual_endstop

[tmc2209 stepper_y]
uart_pin: PC4
diag_pin: ^PG6
run_current: 1.6 # Max current is 2.8 amps, so  x 0.707 x 0.8 is 1.58. 
driver_SGTHRS: 60  # 255 is most sensitive value, 0 is least sensitive. However, tests show that this is the opposite!
home_current: 1
#stealthchop_threshold: 999999
sense_resistor: 0.11

# Driver1
# B motor
[stepper_x]
step_pin: PG0
dir_pin: !PG1
enable_pin: !PF15
microsteps: 32
rotation_distance: 40
full_steps_per_rotation:200
position_endstop: 0
position_max: 150
position_min: 0
homing_speed: 20
endstop_pin: tmc2209_stepper_x:virtual_endstop

[tmc2209 stepper_x]
uart_pin: PD11
diag_pin: ^PG9
run_current: 1.6
driver_SGTHRS: 60
home_current: 1
sense_resistor: 0.11
#stealthchop_threshold: 999999

# Driver2
[stepper_z]
step_pin: PF11
dir_pin: !PG3
enable_pin: !PG5
microsteps: 32
rotation_distance: 4 #4 with new two start, 2mm lead screws
full_steps_per_rotation: 200
endstop_pin: PG10 # endstop 2
position_endstop: 310
position_max: 310
position_min: -3

[tmc2209 stepper_z]
uart_pin: PC6
#diag_pin: PG10
run_current: 0.650
#stealthchop_threshold: 999999
sense_resistor: 0.11

# Driver3
[stepper_z1]
step_pin: PG4
dir_pin: !PC1
enable_pin: !PA0
microsteps: 32
rotation_distance: 4 
full_steps_per_rotation: 200
endstop_pin: PG11 #endstop 3

[tmc2209 stepper_z1]
uart_pin: PC7
#diag_pin: PG11
run_current: 0.650
#stealthchop_threshold: 999999
sense_resistor: 0.11

# Driver4
[extruder]
max_extrude_only_distance: 500.0
max_extrude_only_velocity: 120
max_extrude_cross_section: 5.0
step_pin: EBBcan1:PD0
dir_pin: EBBcan1:PD1
enable_pin: !EBBcan1:PD2
microsteps: 64
rotation_distance: 4.637 # this is the calculated value. 4.637 is default for extruder
full_steps_per_rotation:200
#gear_ratio: 7.5:1
nozzle_diameter: 0.400
filament_diameter: 1.750
heater_pin: EBBcan1:PB13 # HE0
#sensor_type: MAX31865
sensor_type: PT1000
sensor_pin: EBBcan1:PA3
pullup_resistor: 2200
#sensor_pin: EBBcan1: PA4
#spi_bus: spi1
#rtd_nominal_r: 1000
#rtd_reference_r: 4300
#rtd_num_of_wires: 2
control: pid
pid_Kp: 26.630 # tuned 170 C for Rapido ACE
pid_Ki: 6.122
pid_Kd: 28.960
smooth_time: 0.2 #lower value reduces spikes on HIGH accuracy systems, but causes more spikes on low accuracy system. Current fluctautes 3deg c b/c I don't have proper pt1000 amplifier
min_temp: -50
max_temp: 300

[tmc2209 extruder]
uart_pin: EBBcan1:PA15
run_current: 0.5 # Recomended by sherpa mini team is 0.35 max. However I have an ldo stepper high temp with a rated current of 1 amp. That is 0.57 amps nominal. The motor was too hot for me though.
#stealthchop_threshold: 999999
sense_resistor: 0.11

# See page 51 of tmc2209 datasheet for these settings
driver_TBL: 0 # Blanking Time
driver_HEND: 6 # Hysteresis end
driver_HSTRT: 7 # Hysteresis start
driver_TOFF: 4 # Time to slow decay

[force_move]
enable_force_move: False

#[filament_switch_sensor material_0]
#switch_pin: PG12

# Driver5
#[extruder1]
#step_pin: PC13
#dir_pin: PF0
#enable_pin: !PF1
#heater_pin: PA3 # HE1
#sensor_pin: PF5 # T1
#...

#[tmc2209 extruder1]
#uart_pin: PE4
#run_current: 0.800
#stealthchop_threshold: 999999

#[filament_switch_sensor material_1]
#switch_pin: PG13

# Driver6
#[extruder2]
#step_pin: PE2
#dir_pin: PE3
#enable_pin: !PD4
#heater_pin: PB10 # HE2
#sensor_pin: PF6 # T2
#...

#[tmc2209 extruder2]
#uart_pin: PE1
#run_current: 0.800
#stealthchop_threshold: 999999

#[filament_switch_sensor material_2]
#switch_pin: PG14

# Driver7
#[extruder3]
#step_pin: PE6
#dir_pin: PA14
#enable_pin: !PE0
#heater_pin: PB11 # HE3
#sensor_pin: PF7 # T3
#...

#[tmc2209 extruder3]
#uart_pin: PD3
#run_current: 0.800
#stealthchop_threshold: 999999

#[filament_switch_sensor material_3]
#switch_pin: PG15

[heater_bed]
heater_pin: PA1
sensor_pin: PF3 # TB
sensor_type: EPCOS 100K B57560G104F
control: pid
# tuned for stock heater with flex bed with 60 degree Celsius target
pid_Kp: 66.550
pid_Ki: 1.061
pid_Kd: 1043.168
min_temp: 0
max_temp: 110

#[temperature_sensor mcu_temp]
#min_temp: 0
#max_temp: 85
#sensor_type: temperature_mcu
#sensor_mcu: mcu

[temperature_sensor ebb_temp]
min_temp: 0
max_temp: 100
sensor_type: temperature_mcu
sensor_mcu: EBBcan1

#[temperature_sensor host]
#min_temp: 0
#max_temp: 85
#sensor_type: temperature_host

[temperature_sensor chamber]
sensor_pin:  PF4 # T0
sensor_type: ATC Semitec 104NT-4-R025H42G

# part cooling fan
[fan]
pin: EBBcan1:PA1

# hotend fan
[heater_fan hotend_fan]
pin: EBBcan1:PA0
heater: extruder
heater_temp: 50
fan_speed: 1.0

#FAN 0, RPI fan
[temperature_fan RPI_fan]
sensor_type: temperature_host 
pin: PA8                     
shutdown_speed: 0.0
kick_start_time: 0.5
off_below: 0.19
max_speed: 1.0
min_speed: 0.0
max_temp: 80                #Set below 85C, Pi can be damaged at 85C
target_temp: 75
min_temp: 0
control: curve
points:
  40.0, 0.0
  75.0, 1.0
cooling_hysteresis: 5.0


# Fan 1 , blows on the octopus
[temperature_fan controller_fan]
pin: PE5
sensor_type: temperature_mcu
sensor_mcu: mcu
shutdown_speed: 0.0
kick_start_time: 0.5
off_below: 0.19
max_speed: 1.0
min_speed: 0.0
max_temp: 80
target_temp: 75
min_temp: 0
control: curve
points:
  40.0, 0.0
  75.0, 1.0
cooling_hysteresis: 5.0

#[heater_fan fan3]
#pin: PD12

#[heater_fan fan3]
#pin: PD13

#[heater_fan fan4]
#pin: PD14

#[heater_fan fan5]
#pin: PD15

[mcu]
#serial: /dev/serial/by-id/usb-Klipper_stm32f446xx_350011001550335331383520-if00
#restart_method: command
# CAN bus is available on this board. Currently using the usb to can bridge mode
canbus_uuid: 19ac551eac54

# I don't use this unless I am calibrating input shaper
[mcu EBBcan1]
canbus_uuid: 98de018da7fc
# is_non_critical: True. Apparently CAN mcu's can't be non critical. I have to wait for USB upgrade

[printer]
kinematics: corexy
max_velocity: 450
max_accel: 16000
max_z_velocity: 20
max_z_accel: 100
minimum_cruise_ratio: 0.5
square_corner_velocity: 5.0

[board_pins]
aliases:
    # EXP1 header
    EXP1_1=PE8, EXP1_2=PE7,
    EXP1_3=PE9, EXP1_4=PE10,
    EXP1_5=PE12, EXP1_6=PE13,    # Slot in the socket on this side
    EXP1_7=PE14, EXP1_8=PE15,
    EXP1_9=<GND>, EXP1_10=<5V>,

    # EXP2 header
    EXP2_1=PA6, EXP2_2=PA5,
    EXP2_3=PB1, EXP2_4=PA4,
    EXP2_5=PB2, EXP2_6=PA7,      # Slot in the socket on this side
    EXP2_7=PC15, EXP2_8=<RST>,
    EXP2_9=<GND>, EXP2_10=PC5

# See the sample-lcd.cfg file for definitions of common LCD displays.

[display]
lcd_type: st7920
cs_pin: EXP1_7
sclk_pin: EXP1_6
sid_pin: EXP1_8
encoder_pins: ^EXP1_5, ^EXP1_3
click_pin: ^!EXP1_2

[pwm_cycle_time beeper]
pin: EXP1_1
value: 0 # silent at power on
shutdown_value: 0 # disable on emergancy shutdown
cycle_time: 0.001 # 1ms default frequency


# A [probe] section can be defined instead with a pin: setting identical
# to the sensor_pin: for a bltouch

#[neopixel my_neopixel]
#pin: PB0

#*# <---------------------- SAVE_CONFIG ---------------------->
#*# DO NOT EDIT THIS BLOCK OR BELOW. The contents are auto-generated.
#*#
#*# [bed_mesh default]
#*# version = 1
#*# points =
#*# 	  0.097971, 0.056408, 0.012033, 0.000471, 0.035783
#*# 	  0.065158, -0.020154, -0.053904, -0.039842, 0.005471
#*# 	  0.032033, -0.044529, -0.076092, -0.052654, 0.006096
#*# 	  0.000471, -0.076404, -0.117342, -0.080467, -0.009217
#*# 	  -0.018279, -0.097342, -0.107654, -0.066717, 0.004221
#*# tension = 0.2
#*# min_x = 0.0
#*# algo = bicubic
#*# y_count = 5
#*# mesh_y_pps = 2
#*# min_y = 15.0
#*# x_count = 5
#*# max_y = 190.0
#*# mesh_x_pps = 2
#*# max_x = 185.0
#*#
#*# [skew_correction default_skew]
#*# xy_skew = -0.00120614576431
#*# xz_skew = 0.0
#*# yz_skew = 0.0

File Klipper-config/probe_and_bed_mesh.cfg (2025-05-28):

#This file is for probes, bed screws, meshes, and other stuff

[bed_mesh]
speed: 100
horizontal_move_z: 5
mesh_min: 0, 15
mesh_max: 185, 190
probe_count: 5, 5
algorithm: bicubic
fade_start: 1
fade_end: 10

[bed_screws]
# Not accurate. These are probe locations not nozzle locations
screw1: 55,35
screw2: 225,35
screw3: 225,197
screw4: 55,197

[screws_tilt_adjust]
# probe can reach all 4 screws
screw1: 55,35
screw1_name: front left screw
screw2: 225,35
screw2_name: front right screw
screw3: 225,210
screw3_name: rear right screw
screw4: 55,210
screw4_name: rear left screw
horizontal_move_z: 10
speed: 50
screw_thread: CW-M4

[bltouch]
sensor_pin: ^PB7
control_pin: PB6
#probe_with_touch_mode: True
stow_on_each_sample: False
x_offset: -39.5
y_offset: -5.5
z_offset: 1.35
speed: 10.0
samples: 2
samples_tolerance: 0.015
samples_tolerance_retries: 5
sample_retract_dist: 4.0

[safe_z_home]
home_xy_position: 140, 120
speed: 150
z_hop: 5
z_hop_speed: 20

[z_tilt]
#Virtual positions for the pivot points. The nozzle doesn't need to reach it
z_positions: 
    265, 120 # Z motor
    -55, 120 #Z1 motor
#points to probe
points:
    225, 120
    50, 120
retries: 2
retry_tolerance: 0.015

#[homing_override]
#set_position_z:0
#gcode:
#    G1 Z10 F600
#    G28 X Y
#    G1 X166 Y120 F6000
#    G28 Z

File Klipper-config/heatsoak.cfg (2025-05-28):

## 
## HEAT_SOAK HEATER=<heater_name> TARGET=<target_heater_temperature> SOAKER=<heat_soak_temp_sensor_name> [RATE=<heat_soak_temp_rate_of_change>] [TIMEOUT=<time_to_abort_heat_soak>]
##
##
## e.g.
## HEAT_SOAK HEATER=heater_bed TARGET=100 SOAKER="temperature_sensor top_bed"
##
## Based on work by blalor: https://klipper.discourse.group/t/interruptible-heat-soak/1552
##
## Pulled from this guy: https://github.com/garethky/klipper-voron2.4-config/blob/mainline/printer_data/config/heatsoak.cfg

[gcode_macro HEAT_SOAK]
description: Wait for a temperature sensor to reach thermal equilibrium

variable_last_temp: 0
variable_last_soak_temp_rate: None
variable_temp_history: None
variable_smoothed_temp_history: None
variable_stage: "done" ## heating -> soaking -> done -> None
variable_total_time_elapsed: 0
variable_soak_time_remaining: 30
variable_check_interval: 1
variable_heating_report_interval: 2
variable_soaking_report_interval: 5
variable_heater_sensor: None
variable_soaker_sensor: None
variable_target_temp: 0.0
variable_min_soak_temp: 0
variable_target_rate: 0.3
variable_complete: None
variable_cancel: None
variable_temp_smooth_time: 4.0
variable_rate_smooth_time: 20.0
variable_resume_trigger: False
variable_was_print_active: False

gcode:
    { action_respond_info( "Heat Soak starting" )}

    # Soaker is required
    {% set SOAKER = params.SOAKER | string %}
    {% set RATE = params.RATE | default(0.3) | float %} ## in degrees C per minute
    {% set SOAK_TEMP = params.SOAK_TEMP | default(0.0) | float %}
    {% set HEATER = (params.HEATER | string) %} # Optional heater
    {% set TARGET = params.TARGET | default(0) | float %}
    {% set TIMEOUT = (params.TIMEOUT | default(30) | int) * 60 %} ## minutes to seconds
    {% set TEMP_SMOOTH = params.TEMP_SMOOTH | default(4.0) | float %} ## seconds for temp smoothing
    {% set RATE_SMOOTH = params.RATE_SMOOTH | default(20) | float %} ## seconds for rate smoothing
    {% set COMPLETE  = (params.COMPLETE | string) %}
    {% set CANCEL  = (params.CANCEL | string) %}
    {% set HEATING_REPORT_INTERVAL  = params.HEATING_REPORT_INTERVAL | default(2) | int %}
    {% set SOAKING_REPORT_INTERVAL  = params.SOAKING_REPORT_INTERVAL | default(5) | int %}

    # User writeable variables
    SET_GCODE_VARIABLE MACRO=HEAT_SOAK VARIABLE=heater_sensor           VALUE="{HEATER | pprint}"
    SET_GCODE_VARIABLE MACRO=HEAT_SOAK VARIABLE=target_temp             VALUE={TARGET}
    SET_GCODE_VARIABLE MACRO=HEAT_SOAK VARIABLE=min_soak_temp           VALUE={SOAK_TEMP}
    SET_GCODE_VARIABLE MACRO=HEAT_SOAK VARIABLE=soaker_sensor           VALUE="{SOAKER | pprint}"
    SET_GCODE_VARIABLE MACRO=HEAT_SOAK VARIABLE=target_rate             VALUE={RATE}
    SET_GCODE_VARIABLE MACRO=HEAT_SOAK VARIABLE=soak_time_remaining     VALUE={TIMEOUT}
    SET_GCODE_VARIABLE MACRO=HEAT_SOAK VARIABLE=complete                VALUE="'{COMPLETE}'"
    SET_GCODE_VARIABLE MACRO=HEAT_SOAK VARIABLE=cancel                  VALUE="'{CANCEL}'"
    SET_GCODE_VARIABLE MACRO=HEAT_SOAK VARIABLE=temp_smooth_time        VALUE={TEMP_SMOOTH}
    SET_GCODE_VARIABLE MACRO=HEAT_SOAK VARIABLE=rate_smooth_time        VALUE={RATE_SMOOTH}
    SET_GCODE_VARIABLE MACRO=HEAT_SOAK VARIABLE=heating_report_interval VALUE={HEATING_REPORT_INTERVAL}
    SET_GCODE_VARIABLE MACRO=HEAT_SOAK VARIABLE=soaking_report_interval VALUE={SOAKING_REPORT_INTERVAL}

    # Internal variables
    {% set soak_temp = printer[SOAKER].temperature %}
    SET_GCODE_VARIABLE MACRO=HEAT_SOAK VARIABLE=last_temp               VALUE={soak_temp}
    SET_GCODE_VARIABLE MACRO=HEAT_SOAK VARIABLE=temp_history            VALUE="{[soak_temp] | pprint}"
    SET_GCODE_VARIABLE MACRO=HEAT_SOAK VARIABLE=smoothed_temp_history   VALUE="{[] | pprint}"
    SET_GCODE_VARIABLE MACRO=HEAT_SOAK VARIABLE=total_time_elapsed      VALUE=0
    SET_GCODE_VARIABLE MACRO=HEAT_SOAK VARIABLE=last_soak_temp_rate     VALUE=None
    SET_GCODE_VARIABLE MACRO=HEAT_SOAK VARIABLE=check_interval          VALUE=1.0
    SET_GCODE_VARIABLE MACRO=HEAT_SOAK VARIABLE=resume_trigger          VALUE=False
    {% set is_print_active = printer['virtual_sdcard'].is_active or printer['virtual_sdcard'].file_position != 0.0 %}
    SET_GCODE_VARIABLE MACRO=HEAT_SOAK VARIABLE=was_print_active        VALUE={is_print_active}

    # start optional heater
    {% if (HEATER and TARGET != 0.0) %}
        SET_GCODE_VARIABLE MACRO=HEAT_SOAK VARIABLE=stage               VALUE="'heating'"
        SET_HEATER_TEMPERATURE HEATER={HEATER} TARGET={TARGET}
    {% else %}
        SET_GCODE_VARIABLE MACRO=HEAT_SOAK VARIABLE=stage               VALUE="'soaking'"
    {% endif %}

    # pause the print, if active
    {% if is_print_active %}
        PAUSE
    {% endif %}
    
    UPDATE_DELAYED_GCODE ID=_heat_soaker DURATION={check_interval}

[gcode_macro STOP_HEAT_SOAK]
description: stops heat soak activity without running any callbacks
gcode:
    UPDATE_DELAYED_GCODE ID=_heat_soaker DURATION=0  # cancel any pending run
    SET_GCODE_VARIABLE MACRO=HEAT_SOAK VARIABLE=stage VALUE="'done'"

[gcode_macro CANCEL_HEAT_SOAK]
description: cancels an in-progress HEAT_SOAK cycle and runs the cancel callback
gcode:
    # check that the HEAT_SOAK macro is active before canceling
    {% set heat_soak = printer['gcode_macro HEAT_SOAK'] %}
    {% set stage = heat_soak.stage %}
    {% if stage in ("heating", "soaking") %}
        STOP_HEAT_SOAK
        {% if heat_soak.cancel %}
            {heat_soak.cancel}
        {% endif %}
    {% endif %}

[gcode_macro HEAT_SOAK_RESUME]
description: Resume while heat soaking results in the soaking phase being skipped, any complete callback is run
gcode:
    {% set ON_RESUME = (params.ON_RESUME | default("_HEAT_SOAK__BASE_RESUME")) | string %}
    {% set heat_soak = printer['gcode_macro HEAT_SOAK'] %}
    {% set stage = heat_soak.stage %}
    {% if stage == "heating"  %}
        SET_GCODE_VARIABLE MACRO=HEAT_SOAK VARIABLE=resume_trigger VALUE=True
    {% elif stage == "soaking" %}
        STOP_HEAT_SOAK
        {% if heat_soak.complete %}
            {heat_soak.complete}
        {% endif %}
        {ON_RESUME} {% for p in params %}{'%s=%s ' % (p, params[p])}{% endfor %}
    {% else %}
        {ON_RESUME} {% for p in params %}{'%s=%s ' % (p, params[p])}{% endfor %}
    {% endif %}

[gcode_macro RESUME]
description: Resume while heat soaking results in the soaking phase being skipped, any complete callback is run
rename_existing: _HEAT_SOAK__BASE_RESUME
gcode:
    HEAT_SOAK_RESUME ON_RESUME=_HEAT_SOAK__BASE_RESUME
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

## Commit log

2025-03-06 Updated Log with logo ideas and frame
2025-03-09 Finished Logo Design
    [Meteoroid-logo-3DP.dxf]
2025-03-10 Added Frame Stiffener
2025-03-18 Add Z-axis rails to frame
2025-03-19 Start bed frame design
2025-03-23 Updated Icon
    [Meteoroid-logo-3DP.dxf]
2025-03-25 Added main CAD file, finished base frame
2025-03-28 Finished x axis, changed color scheme
    forgot to commit it yesterday though!
2025-03-28 Updated CAD step files with latest colors and x joint
    [MGN12 Rail 350mm.step, X axis.step, bottom electronics parts.step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]
2025-03-29 3 Days Left! Finished main motion, still need toolheads
2025-03-31 Finished toolhead carriage and lock
2025-04-03 Finished Toolhead design
    [toolhead carriage.step]
2025-04-05 Pre-prep for v0.5
    [2.54 mm DUPONT MALE PIN HEADER, IO, 2X20, RPi4ModelB.SLDPRT, 2.54 mm DUPONT MALE PIN HEADER, IO, 2X40, RPi4ModelB.SLDPRT, 2.54 mm DUPONT MALE PIN HEADER, POE, 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]
2025-04-06 Push for v0.5
    added pcb and docs
    [BOM_Main assembly_simplified.csv, Battery Balancer.kicad_sch, Battery Charger.kicad_sch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]
2025-04-06 Updated BOM
    [BOM_Main assembly_simplified.csv]
2025-04-07 Redesigned XY Gantry
    [Front Tensioning Plate - Tensioner Platex2.stl, Front Tensioning Plate.step, Left Tensioner.step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]
2025-04-21 Minor clearance changes
    [Motor Mounts - Left Motor Mount Top.step, Motor Mounts - Left Motor Mount.step, Motor Mounts - Right Motor Mount Top.step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]
2025-04-21 Updated changelog
    [BOM_Main assembly_simplified.csv]
2025-04-21 Started printer file config
    [ZeroG Callibration print ABS.stl]
2025-04-21 Adjusted tolerances
    [Front Tensioning Plate.step, Motor Mounts - Left Motor Mount Top.step, Motor Mounts - Left Motor Mount.step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]
2025-04-22 Fixed toolhead missing lock entrance
    [Toolhead carriage - Carraige - Belt clampx2.step, Toolhead carriage - Carraige - Rail mount.step, Toolhead carriage - Carraige - back plate.step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]
2025-05-04 Redesigned toolhead
    [Rapido 2 UHF + Orbitor 2.5 Toolhead - Curve 1.step, Rapido 2 UHF + Orbitor 2.5 Toolhead - Curve 2.step, Rapido 2 UHF + Orbitor 2.5 Toolhead - Curve 3.step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]
2025-05-04 Made ducts thinner
    [Rapido 2 UHF + Orbitor 2.5 Toolhead - Curve 1.step, Rapido 2 UHF + Orbitor 2.5 Toolhead - Curve 2.step, Rapido 2 UHF + Orbitor 2.5 Toolhead - Curve 3.step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]
2025-05-04 Updated print project
2025-05-06 Fixed motor mount hole size
    It was too small to account for a rim on the motor
    [Left motor mount.step, Right motor mount.step]
2025-05-12 Added Chamber
    [Chamber panel.step, Motor Mounts - Left Motor Mount Top.step, Motor Mounts - Left Motor Mount.step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]
2025-05-28 Getting ready for v0.7
    [2.54 mm DUPONT MALE PIN HEADER, IO, 2X20, RPi4ModelB.SLDPRT, 2.54 mm DUPONT MALE PIN HEADER, IO, 2X40, RPi4ModelB.SLDPRT, 2.54 mm DUPONT MALE PIN HEADER, POE, 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]
2025-07-10 first prototype of push push lock
    [Base Tool.step, Toolhead carriage.step]
2025-07-10 2nd prototype push push lock
    [Base Tool.step, Toolhead carriage.step]
2025-07-10 rotated springs 90 degrees, redesigned tracks slightly
    [Base Tool.step, Toolhead carriage.step]
2025-07-10 fixed track gap
    [Base Tool.step, Toolhead carriage.step]
2025-07-10 added teardrops to lock block
    [Base Tool.step]
2025-07-10 re-added mounting contacts, tweaked clearances
    [Base Tool.step, Toolhead carriage.step]
2026-04-25 Complete hotswap power & data board design
    IDK why I didn't commit this until now
    [BOM-Toolset Hotswap Board.csv, Data Protection.kicad_sch, TPS2491.DSN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]
2026-04-25 Massive CAD file dump from a year
    [Base Tool - Base Tool.step, Base Tool - lock block.step, Base Tool - pusher bar.step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]
2026-04-25 Minor tweaks to adapter PCB from while back
    [Battery Balancer.kicad_sch, Battery Charger.kicad_sch]

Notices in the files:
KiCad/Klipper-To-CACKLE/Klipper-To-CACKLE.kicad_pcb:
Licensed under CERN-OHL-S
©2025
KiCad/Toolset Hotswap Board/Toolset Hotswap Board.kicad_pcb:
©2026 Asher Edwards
